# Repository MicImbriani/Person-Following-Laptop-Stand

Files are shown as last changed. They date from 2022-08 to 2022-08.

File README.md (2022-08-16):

# Person-Following Laptop Stand

<h1>Overview</h1>
Built a robot that takes a laptop placed on top, and follows the user left/right and up/down using the laptop's camera.
The purpose for this device is to keep the user centered during online meetings and calls, which are nowadays increasingly more common.
The device uses DC motors for the lateral movement, and a mechanism (a lead scew attached to a DC motor) for the vertical movement.
More details below.

- The 3D modeling was done using Fusion360.
- The models were 3D printed using Cura software, and 3D-printed using Prusa i3 Mk3 printer.
- All wooden parts are in MDF, and were laser cut.
- The code was written in Python and Arduino.
- The electronics' schematics were done using Fritzing.






# The robot is divided into two levels: upper and lower. 

<h2>Lower Level</h2>

LOWER

In the lower level, the wheeilng system is placed: this is used for the left/right movement. Instead of directly attaching the wheels to the motors, a gearing system (2 gears, 1:1 ratio) was used in combination with a 3D-printed component with 2 radial ball bearings in ints inside: this allowed to transfer the weight load from the motors' shafts to the device.
activeWheel
activeWheelOpen

There is also a mechanism (composed of a DC motor and a lead screw) for the up/down movement: this mechanism will move the base at the top of the device on which the laptop is placed.
12motor

Finally, two IR sensors are placed at the extremities of the device, which are used for edge detection and preventing the robot from falling off of the surface on which it is placed.

<h2>Upper Level</h2>
 
UPPERFLOOR

In the upper level, the Arduino, breadboard and AC/DC converter (or, if connecting the robot to an electric outlet is not feasible, a battery) are placed.
Two IR sensors are also placed for preventing the base from moving too high or too low. An extra component is installed to maintain the rotation of the lead screw centred. 


Guiding rods are installed at the four corners of the upper level: their purpose is to maintain the fixed orientation of the base, which  in turn enables the lead screw to move the base up and down. These guiding rods work in combination with the rods that are fixed underneath the laptop base. Additionally, a 3D-printed component is also fixed to enable the transfering of the lead screw's rotational work into linear vertical movement of the base.


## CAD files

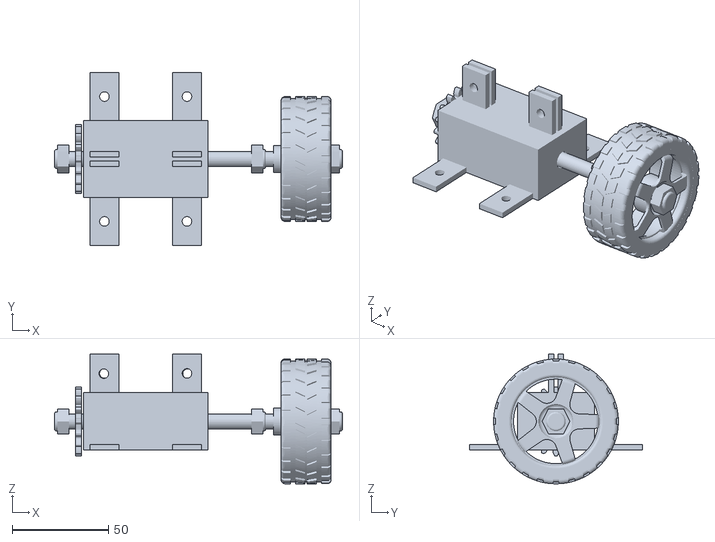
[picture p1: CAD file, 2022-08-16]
CAD Design Files/Wheel System/Active Wheels/ASSEMBLY+Active+Wheels.stl
150.0 x 90.0 x 67.5

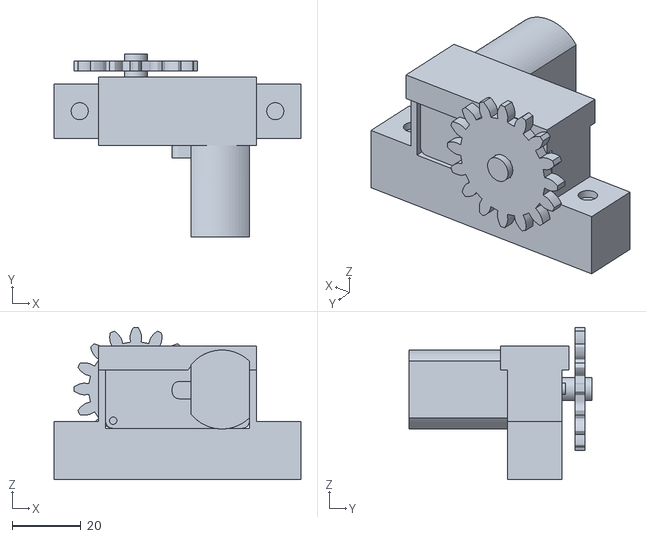
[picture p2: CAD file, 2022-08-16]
CAD Design Files/Wheel System/Motors/ASSEMBLY+motors+and+holders.stl
72.0 x 53.3 x 44.4

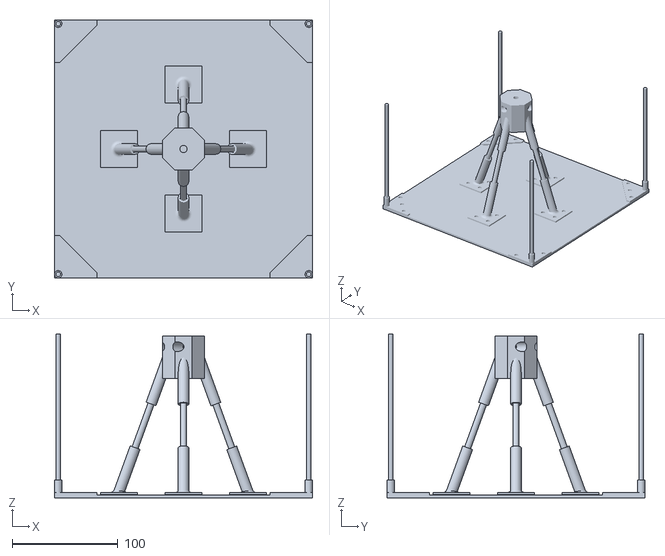
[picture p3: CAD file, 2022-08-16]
CAD Design Files/Upper Floor/ASSEMBLY+Laptop+Base.stl
244.0 x 244.0 x 155.0

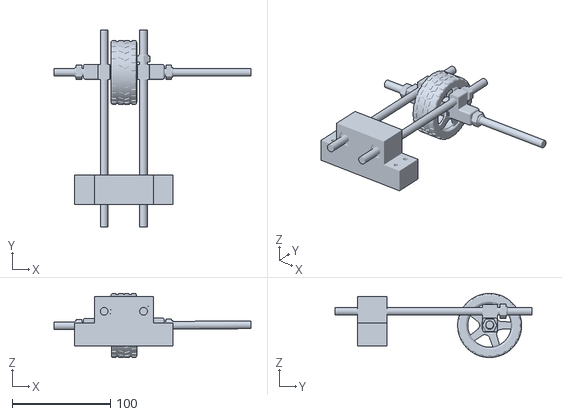
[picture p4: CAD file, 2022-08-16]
CAD Design Files/Wheel System/Passive Wheels/ASSEMBLY+Passive+Wheels.stl
200.0 x 200.0 x 65.1

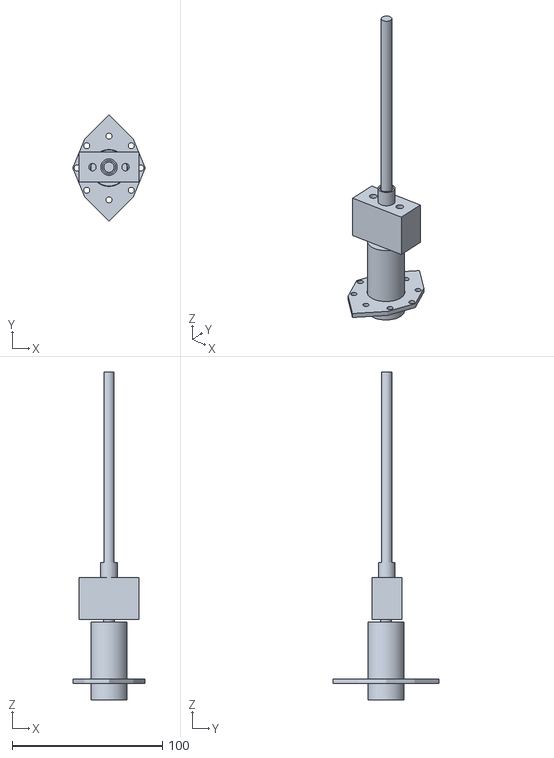
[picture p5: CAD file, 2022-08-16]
CAD Design Files/Lower Floor/Mechanism/ASSEMBLY+Motor+12V.stl
48.1 x 70.7 x 218.5

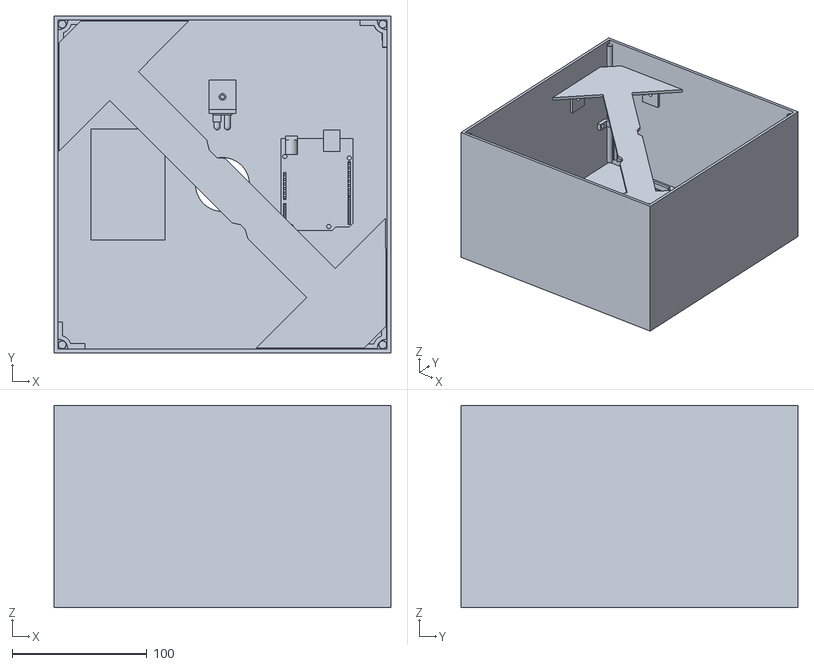
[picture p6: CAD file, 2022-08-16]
CAD Design Files/Upper Floor/ASSEMBLY+Upper+floor.stl
250.0 x 250.0 x 150.0

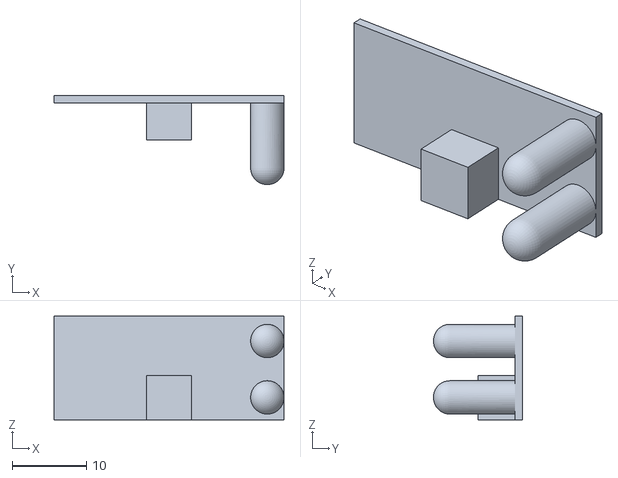
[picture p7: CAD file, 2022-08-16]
CAD Design Files/Lower Floor/IR_sensor.stl
31.0 x 12.0 x 14.0

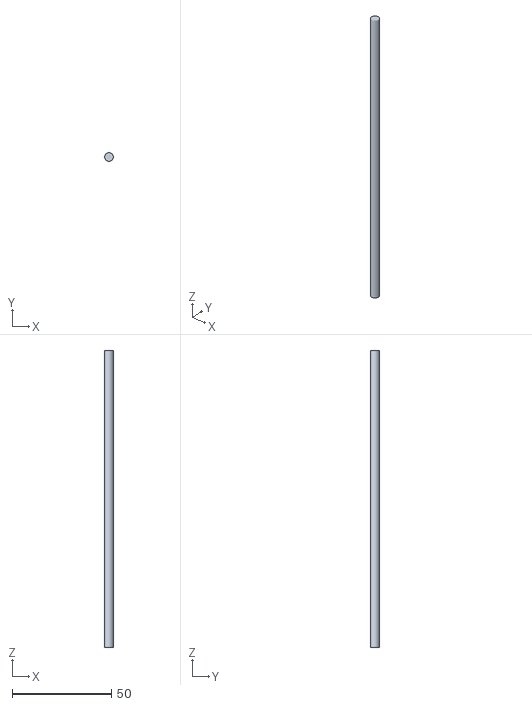
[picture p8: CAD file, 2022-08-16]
CAD Design Files/Upper Floor/Rods.stl
4.40 x 4.40 x 150.0

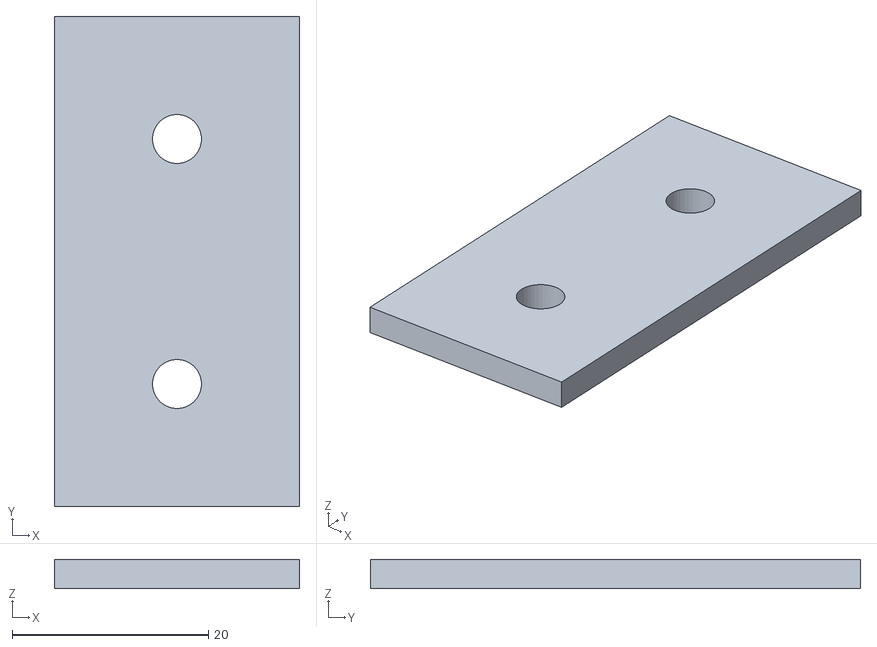
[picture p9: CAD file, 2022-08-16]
CAD Design Files/WallHolder.stl
25.0 x 50.0 x 3.00

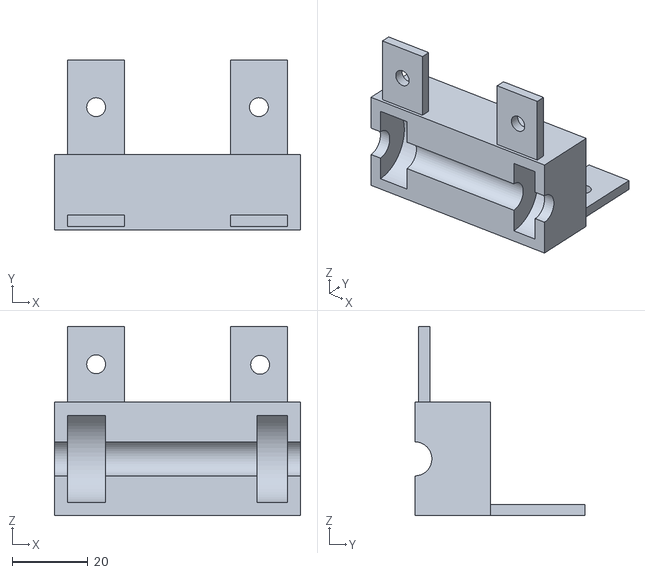
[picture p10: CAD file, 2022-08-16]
CAD Design Files/Wheel System/Active Wheels/BearingsHolder.stl
65.0 x 45.0 x 50.0

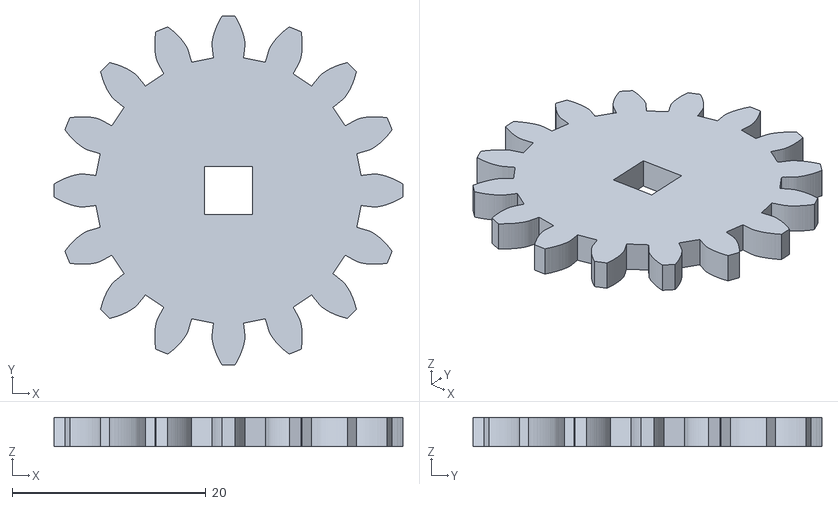
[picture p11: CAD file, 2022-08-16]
CAD Design Files/Wheel System/Motors/Gear+Motor.stl
36.0 x 36.0 x 3.00

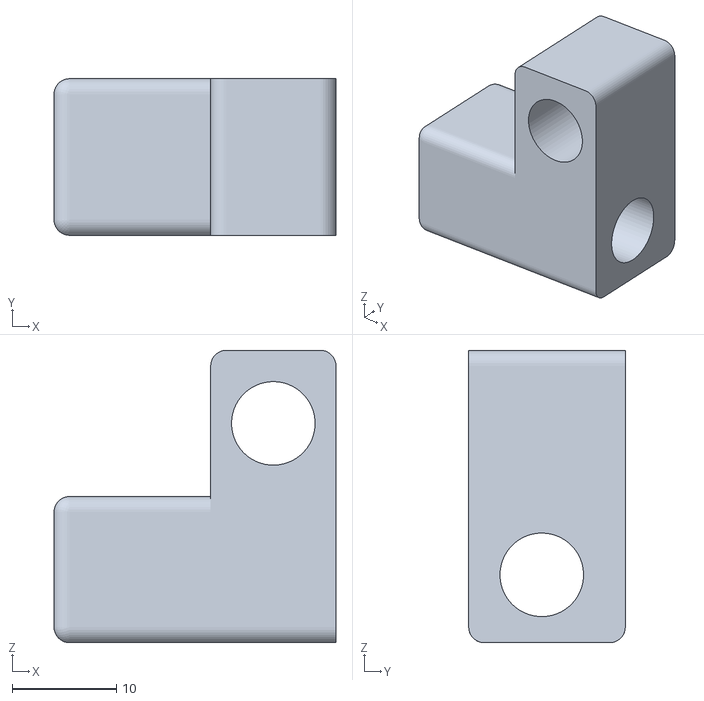
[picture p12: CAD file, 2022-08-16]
CAD Design Files/Wheel System/Passive Wheels/SupportWheelsConnector.stl
27.0 x 15.0 x 28.0

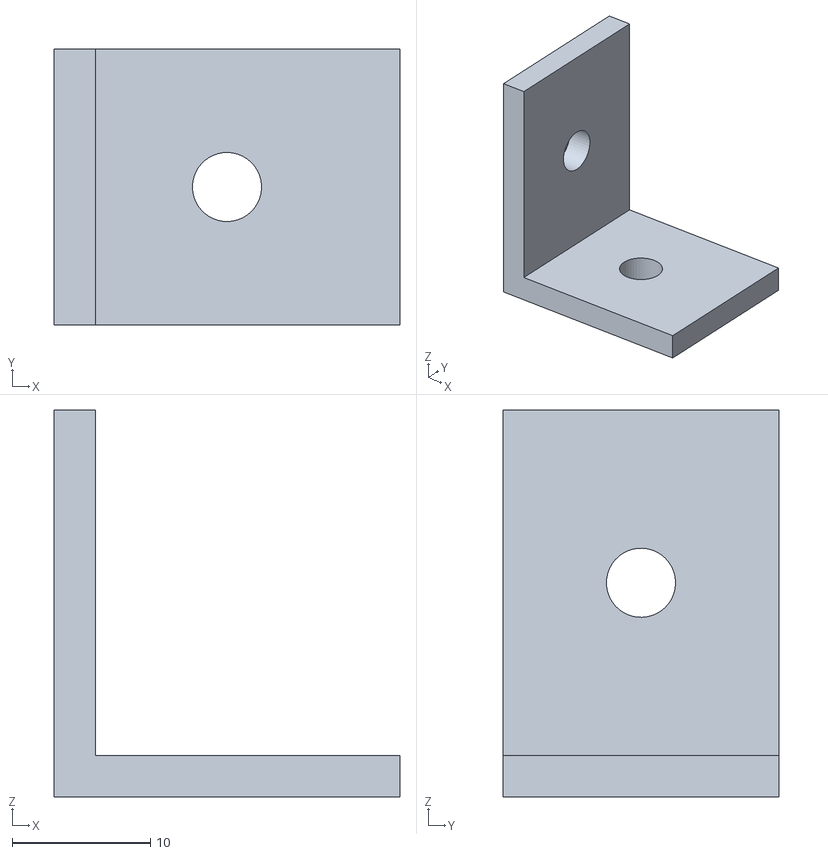
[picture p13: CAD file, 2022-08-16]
CAD Design Files/BaseHolder.stl
25.0 x 20.0 x 28.0

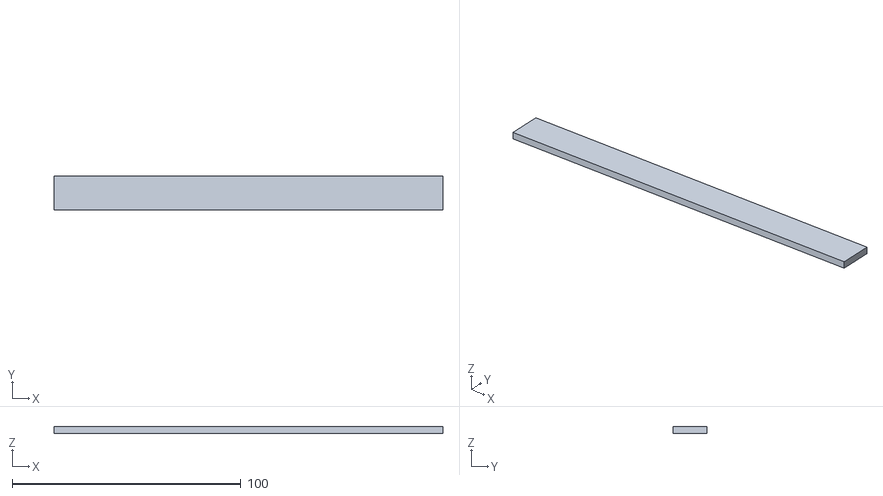
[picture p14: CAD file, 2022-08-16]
CAD Design Files/Lower Floor/IR+Sensor+Stick.stl
170.0 x 15.0 x 3.00

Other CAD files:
CAD Design Files/Lower Floor/Mechanism/ROD+motor+holders.stl
CAD Design Files/Wheel System/Active Wheels/M8+Nut.stl
CAD Design Files/Wheel System/Motors/MotorHoldersSupport.stl
CAD Design Files/Wheel System/Passive Wheels/Wheel.stl
CAD Design Files/Lower Floor/Mechanism/LEAD_SCREW.stl
CAD Design Files/Lower Floor/Mechanism/LeadScrewHolder.stl
CAD Design Files/Lower Floor/Mechanism/LeadScrewRotator.stl
CAD Design Files/Lower Floor/Mechanism/Motor+130RPM12V.stl
CAD Design Files/Lower Floor/Mechanism/MotorHolder_DOWN.stl
CAD Design Files/Lower Floor/Mechanism/MotorHolder_UP.stl
CAD Design Files/Lower Floor/Mechanism/ROD+motor+holder+to+base.stl
CAD Design Files/Upper Floor/ASSEMBLY+Lead+Screw+Stabilizer.stl
CAD Design Files/Upper Floor/Breadboard.stl
CAD Design Files/Upper Floor/GuideRodHeads.stl
CAD Design Files/Upper Floor/GuidelineHolder.stl
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

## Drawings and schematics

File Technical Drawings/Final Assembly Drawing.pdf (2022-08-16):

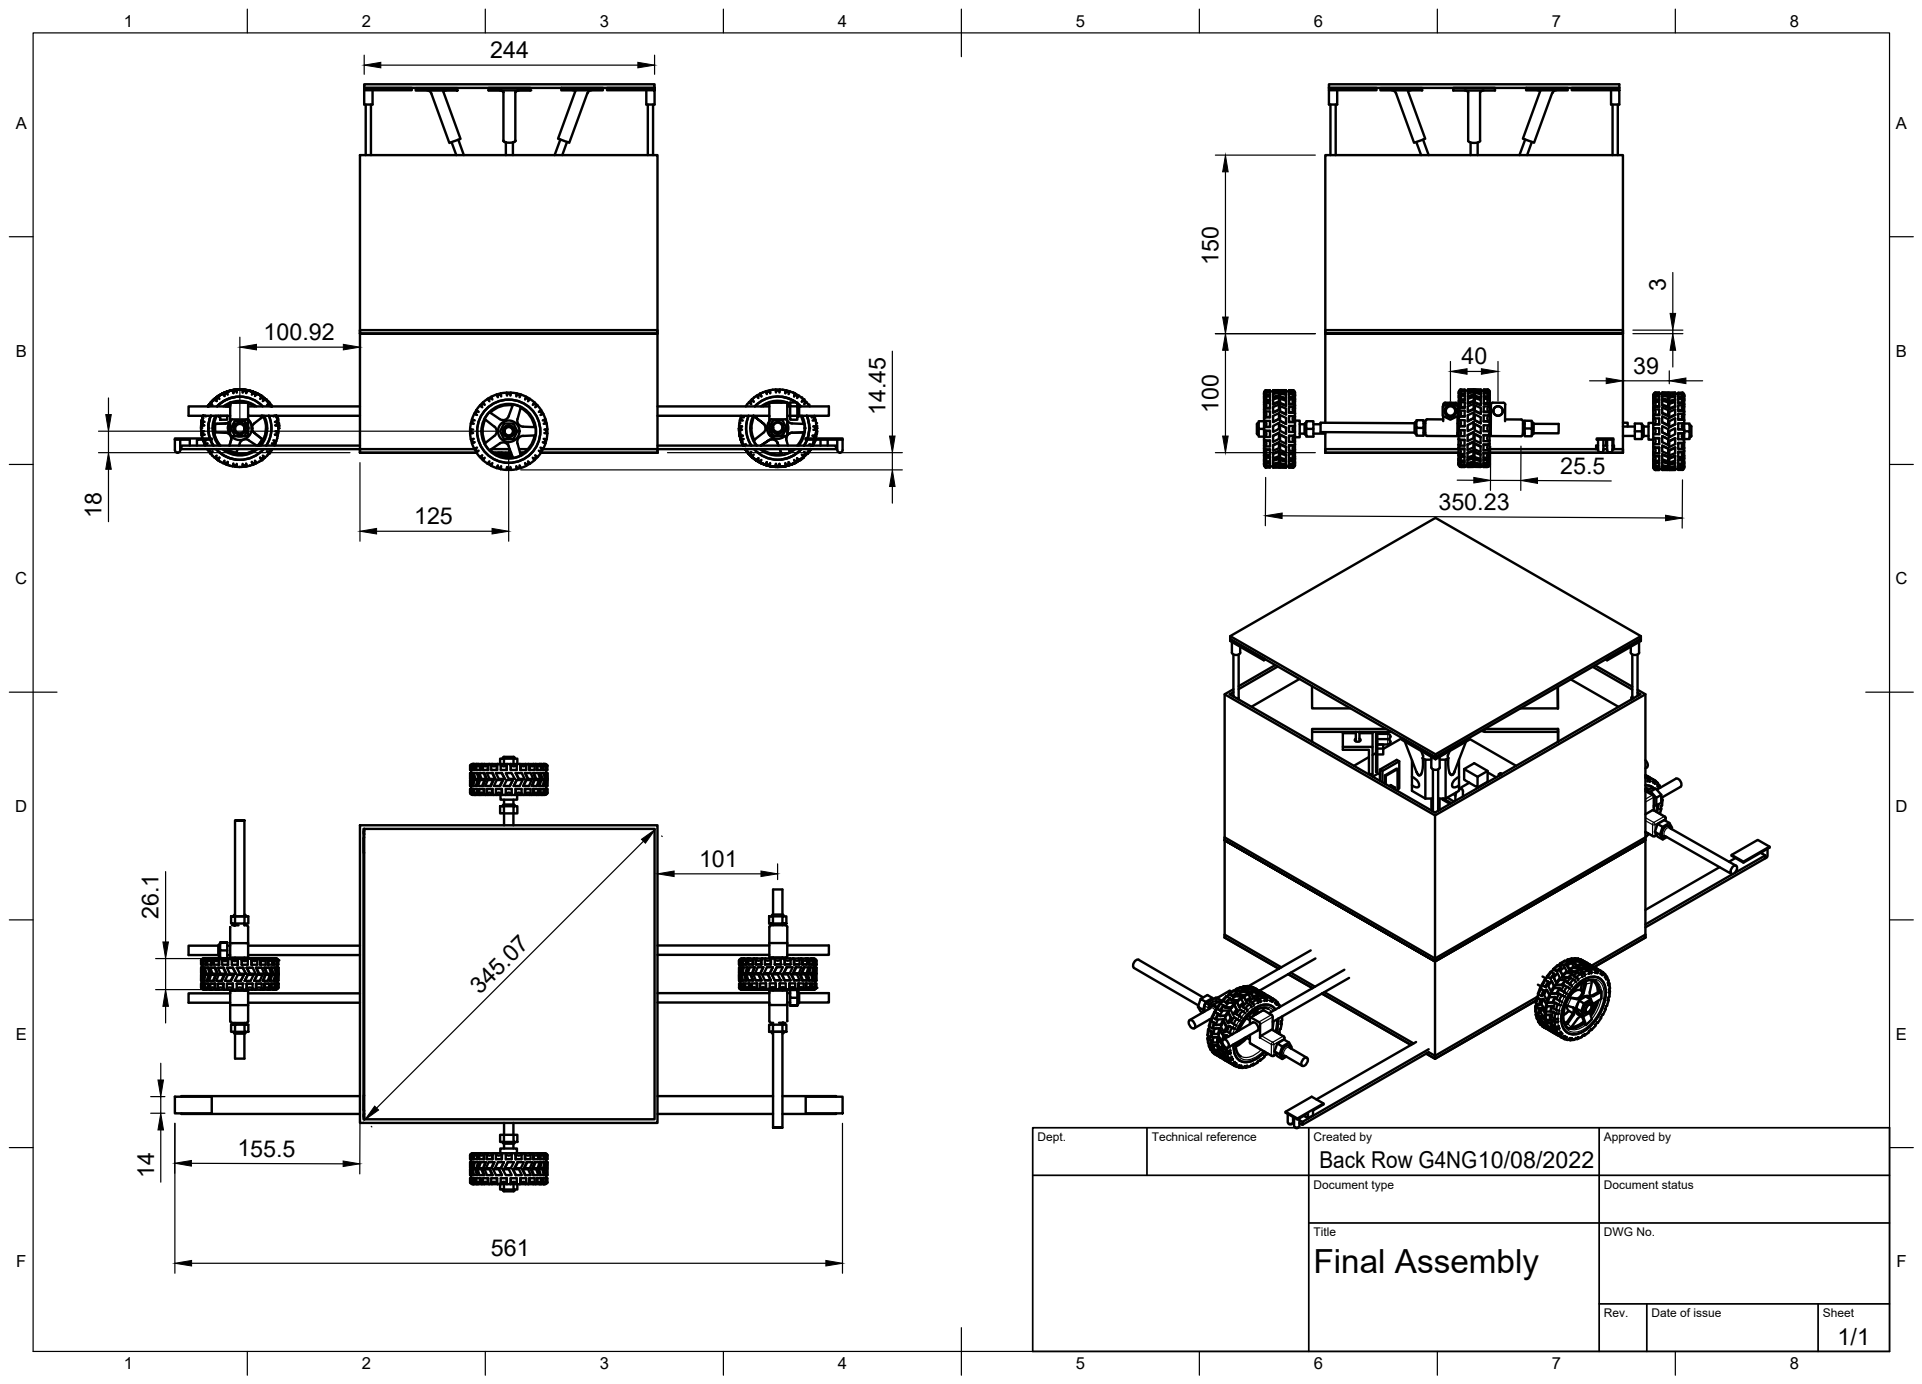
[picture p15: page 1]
Dept.; Technical reference; Created by; Approved by; Document type; Document status; Title; DWG No.; Rev.; Date of issue; Sheet; Final Assembly; Back Row G4NG

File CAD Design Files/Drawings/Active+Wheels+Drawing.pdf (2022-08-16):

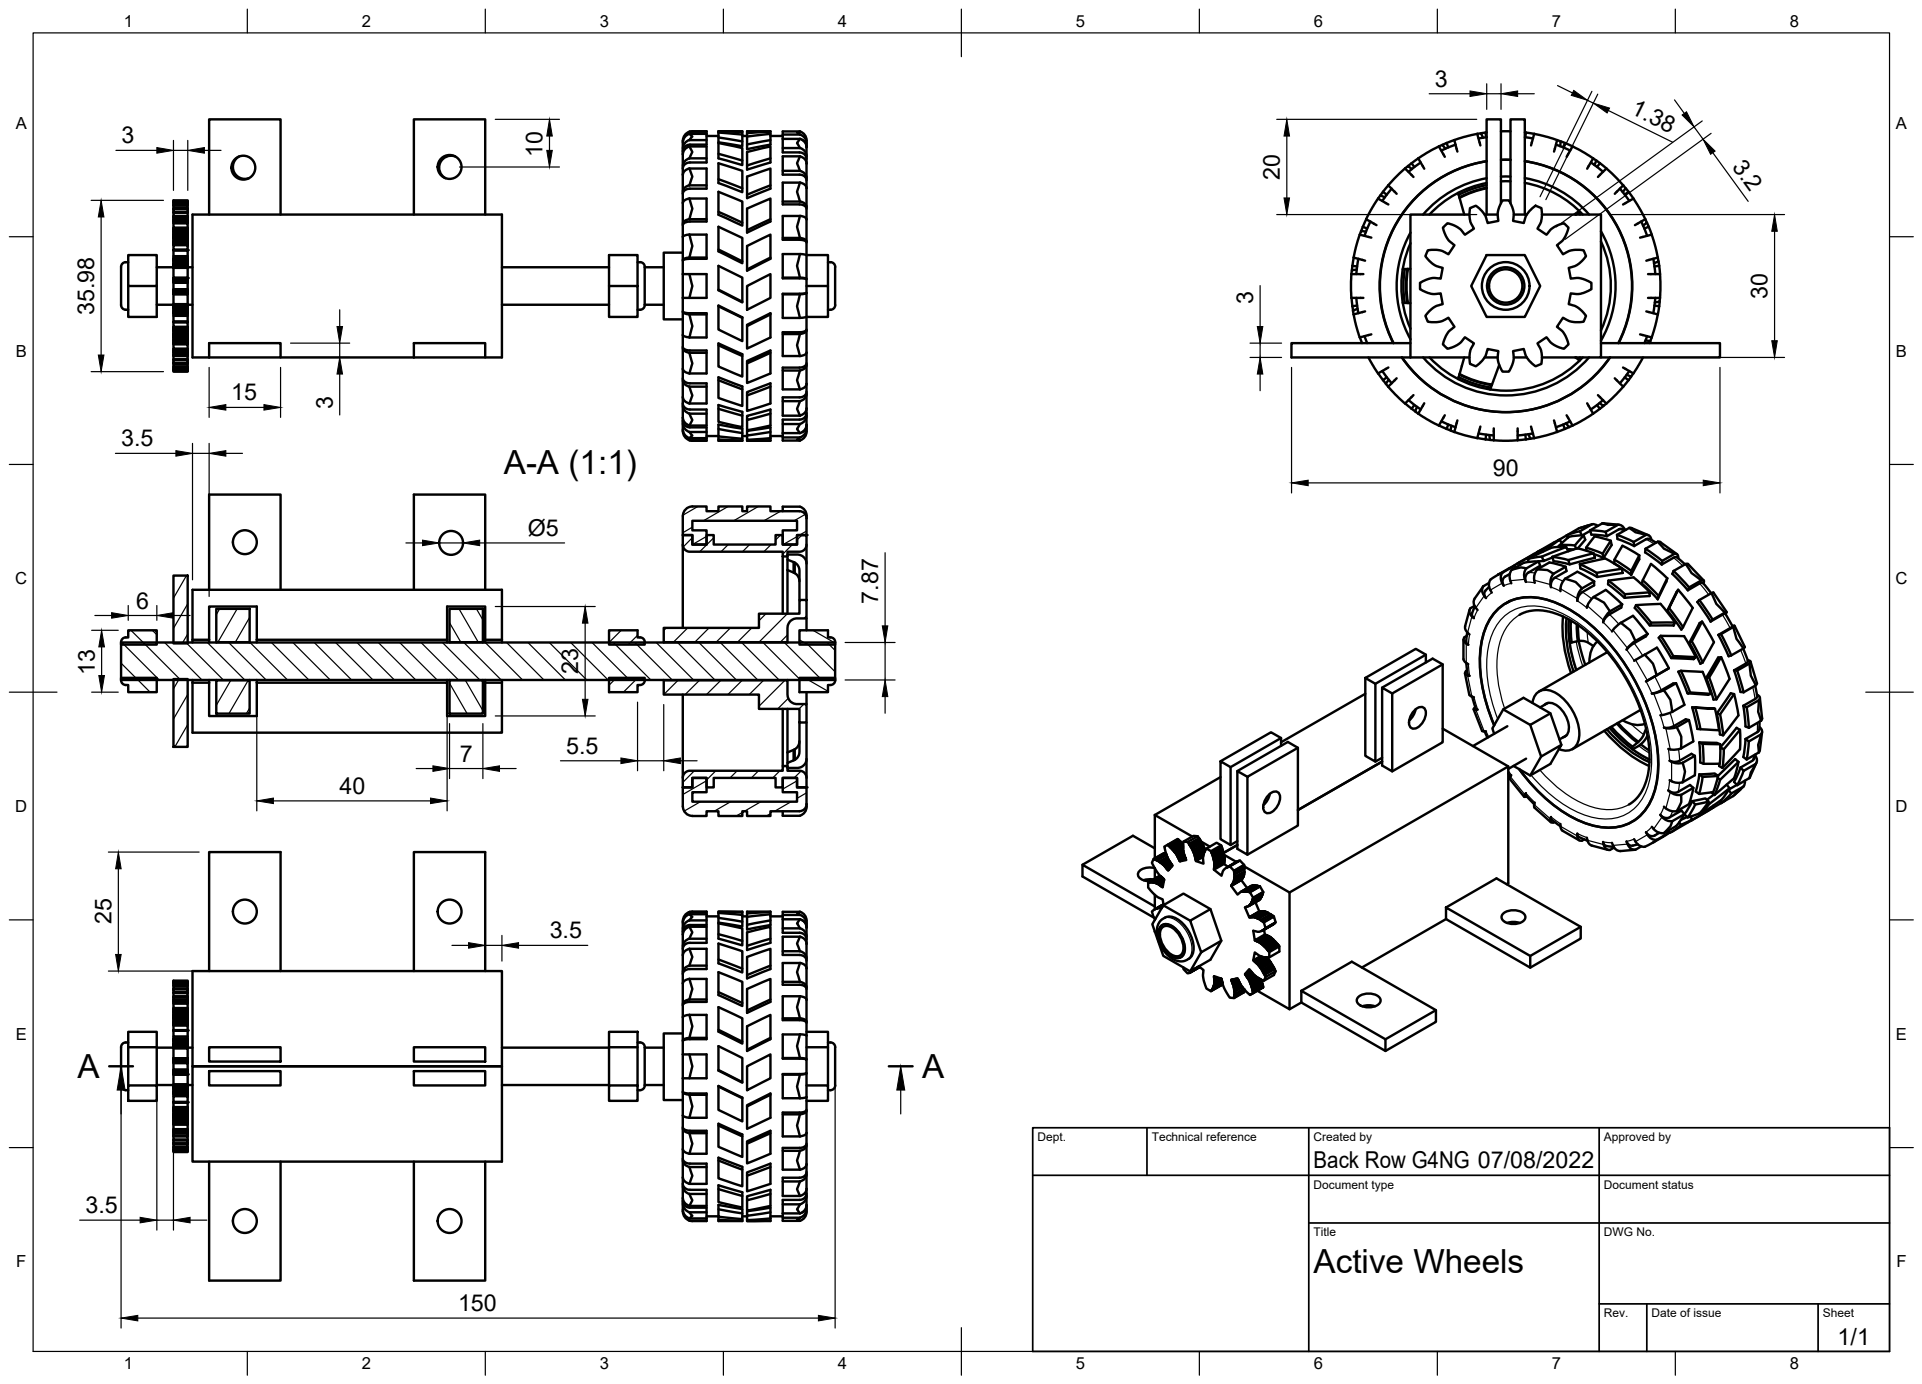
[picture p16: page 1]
Title; DWG No.; Rev.; Date of issue; Sheet; Active Wheels

Dept. | Technical reference | Created by Back Row G4NG 07/08/2022 | Approved by

Document type | Document status

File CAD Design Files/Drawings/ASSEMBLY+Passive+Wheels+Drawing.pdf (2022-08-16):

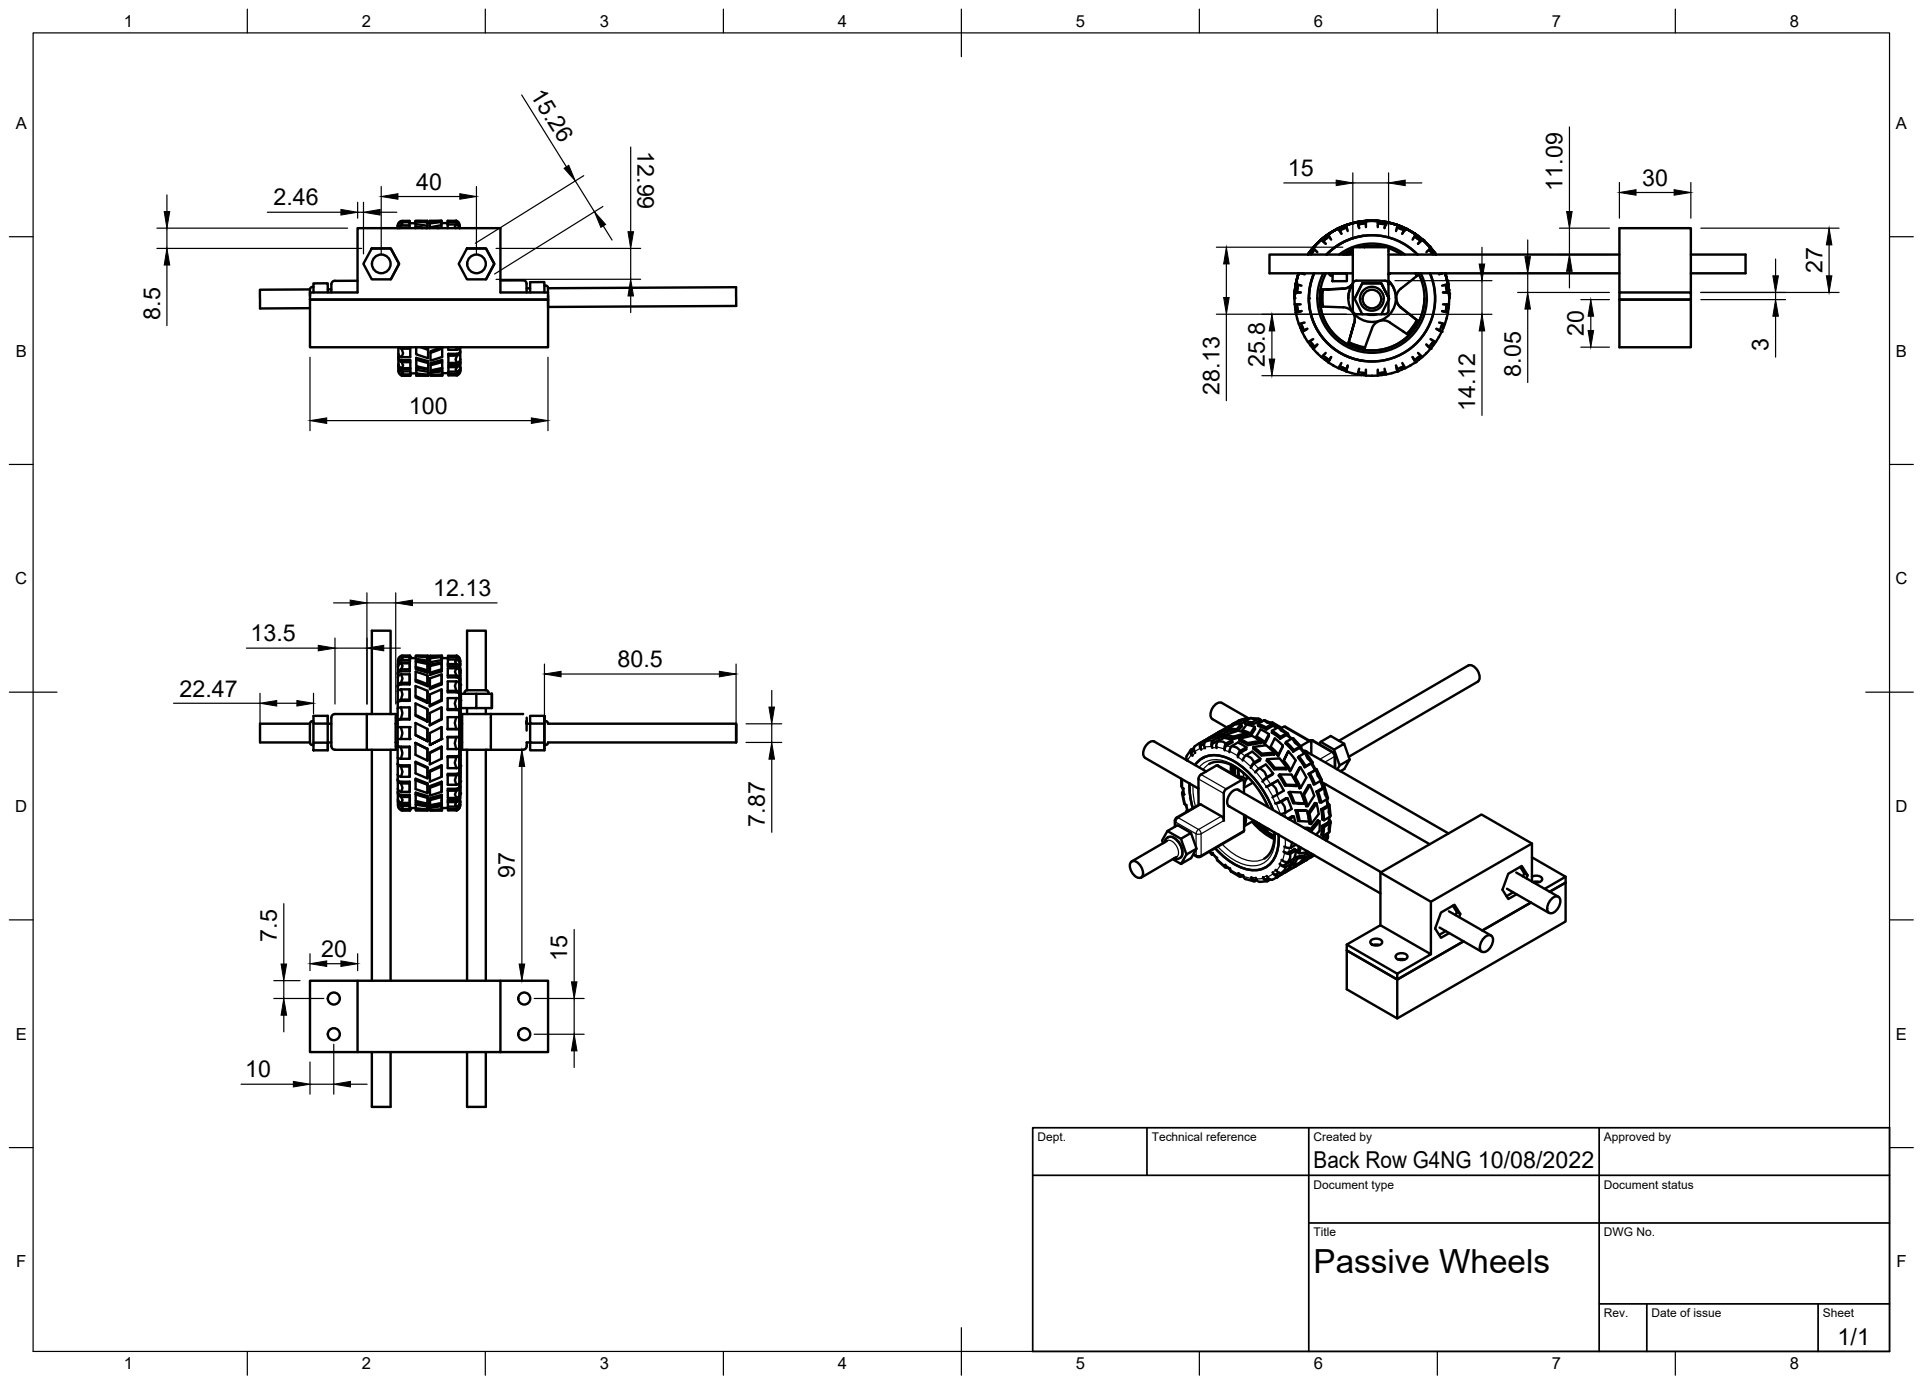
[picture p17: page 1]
Title; DWG No.; Rev.; Date of issue; Sheet; Passive Wheels

Dept. | Technical reference | Created by Back Row G4NG 10/08/2022 | Approved by

Document type | Document status

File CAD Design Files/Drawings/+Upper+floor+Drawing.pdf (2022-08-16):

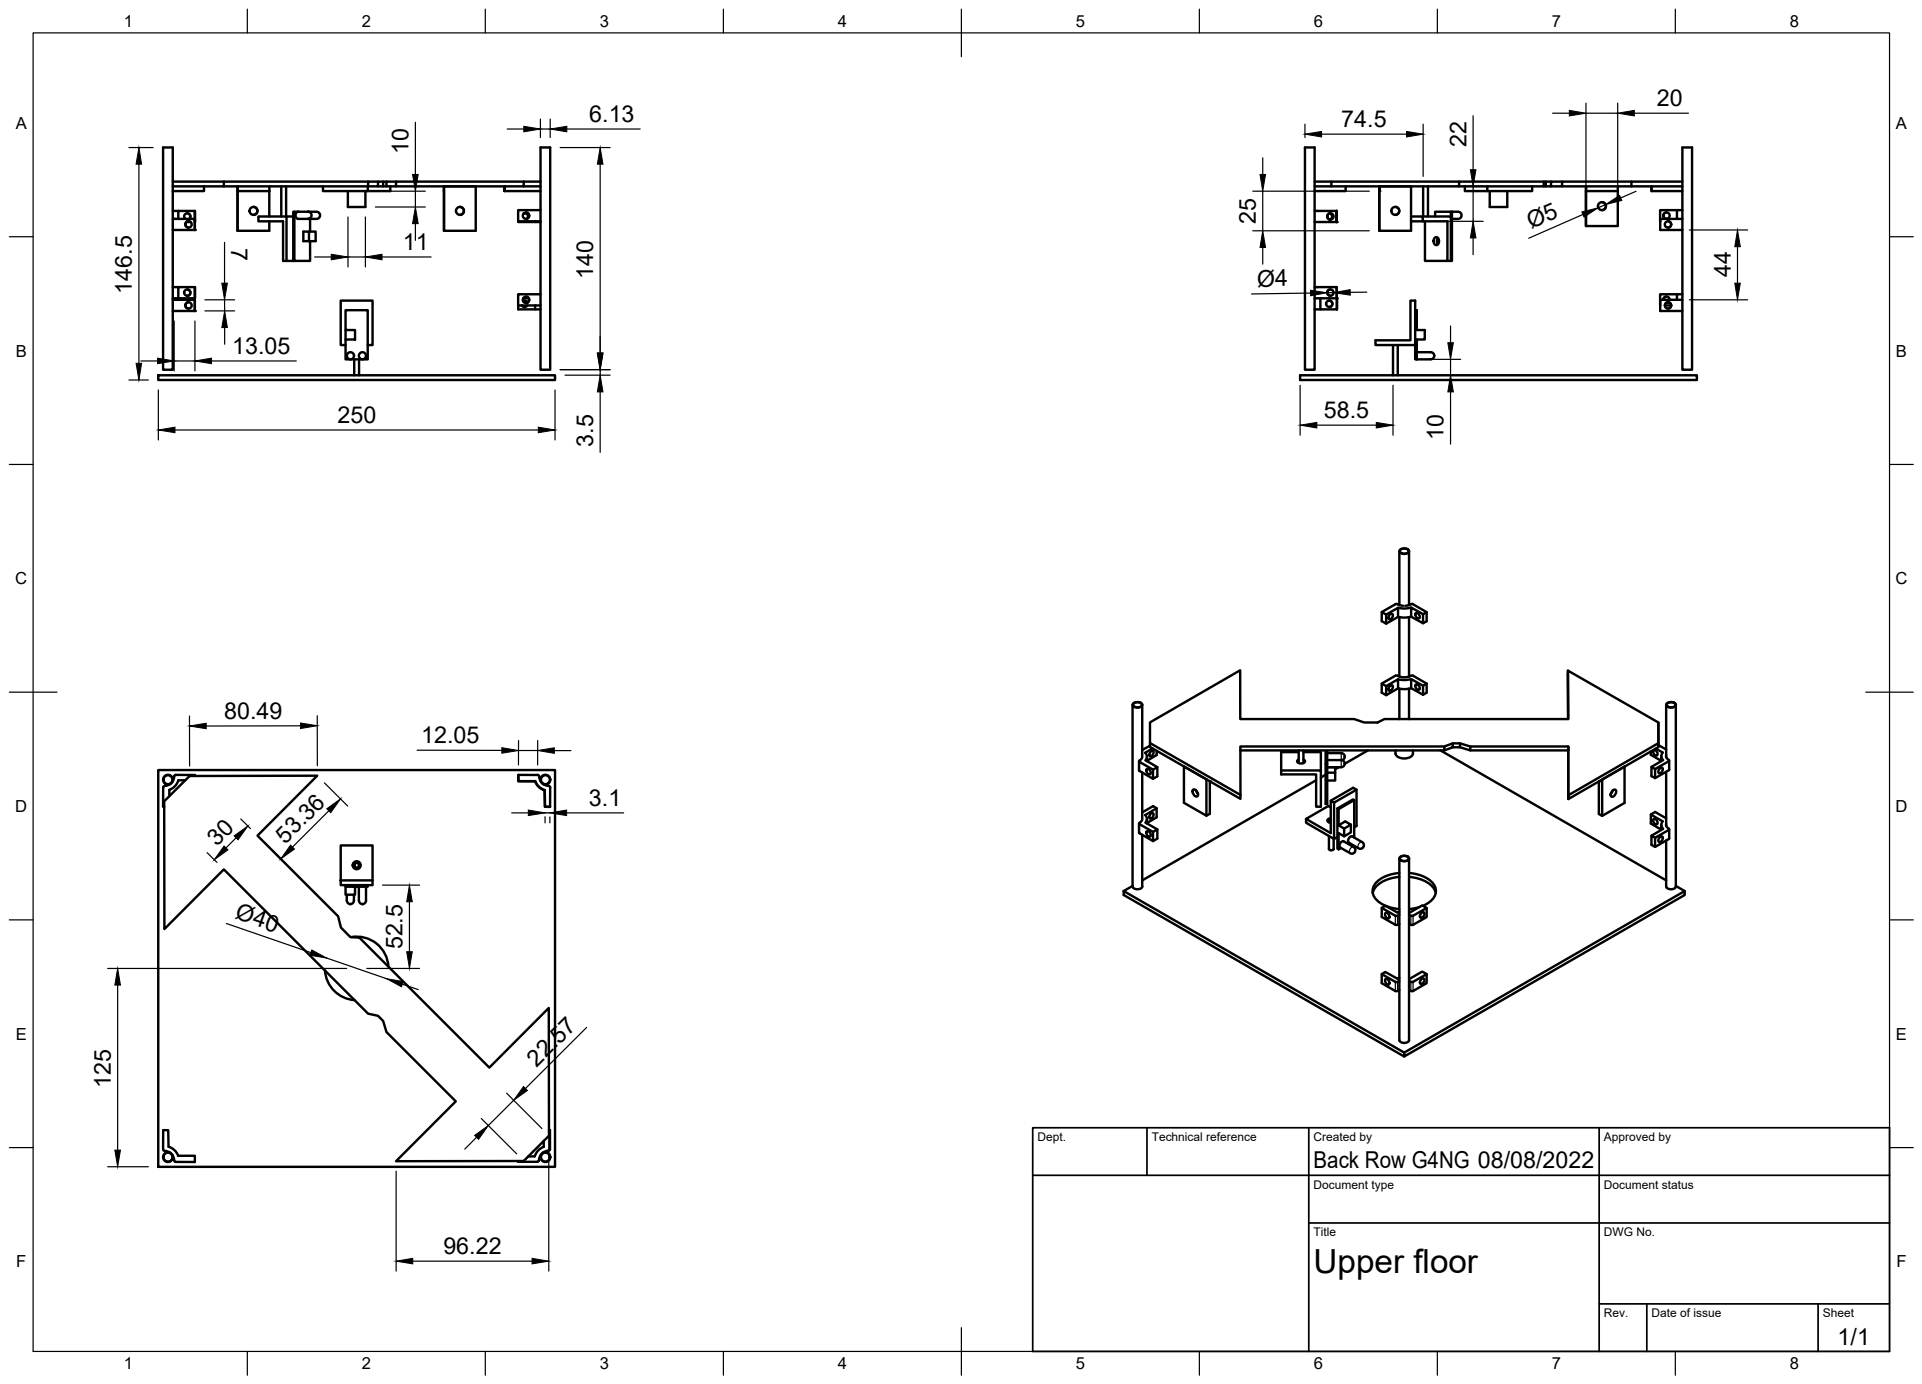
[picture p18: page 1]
Title; DWG No.; Rev.; Date of issue; Sheet; Upper floor

Dept. | Technical reference | Created by Back Row G4NG 08/08/2022 | Approved by

Document type | Document status

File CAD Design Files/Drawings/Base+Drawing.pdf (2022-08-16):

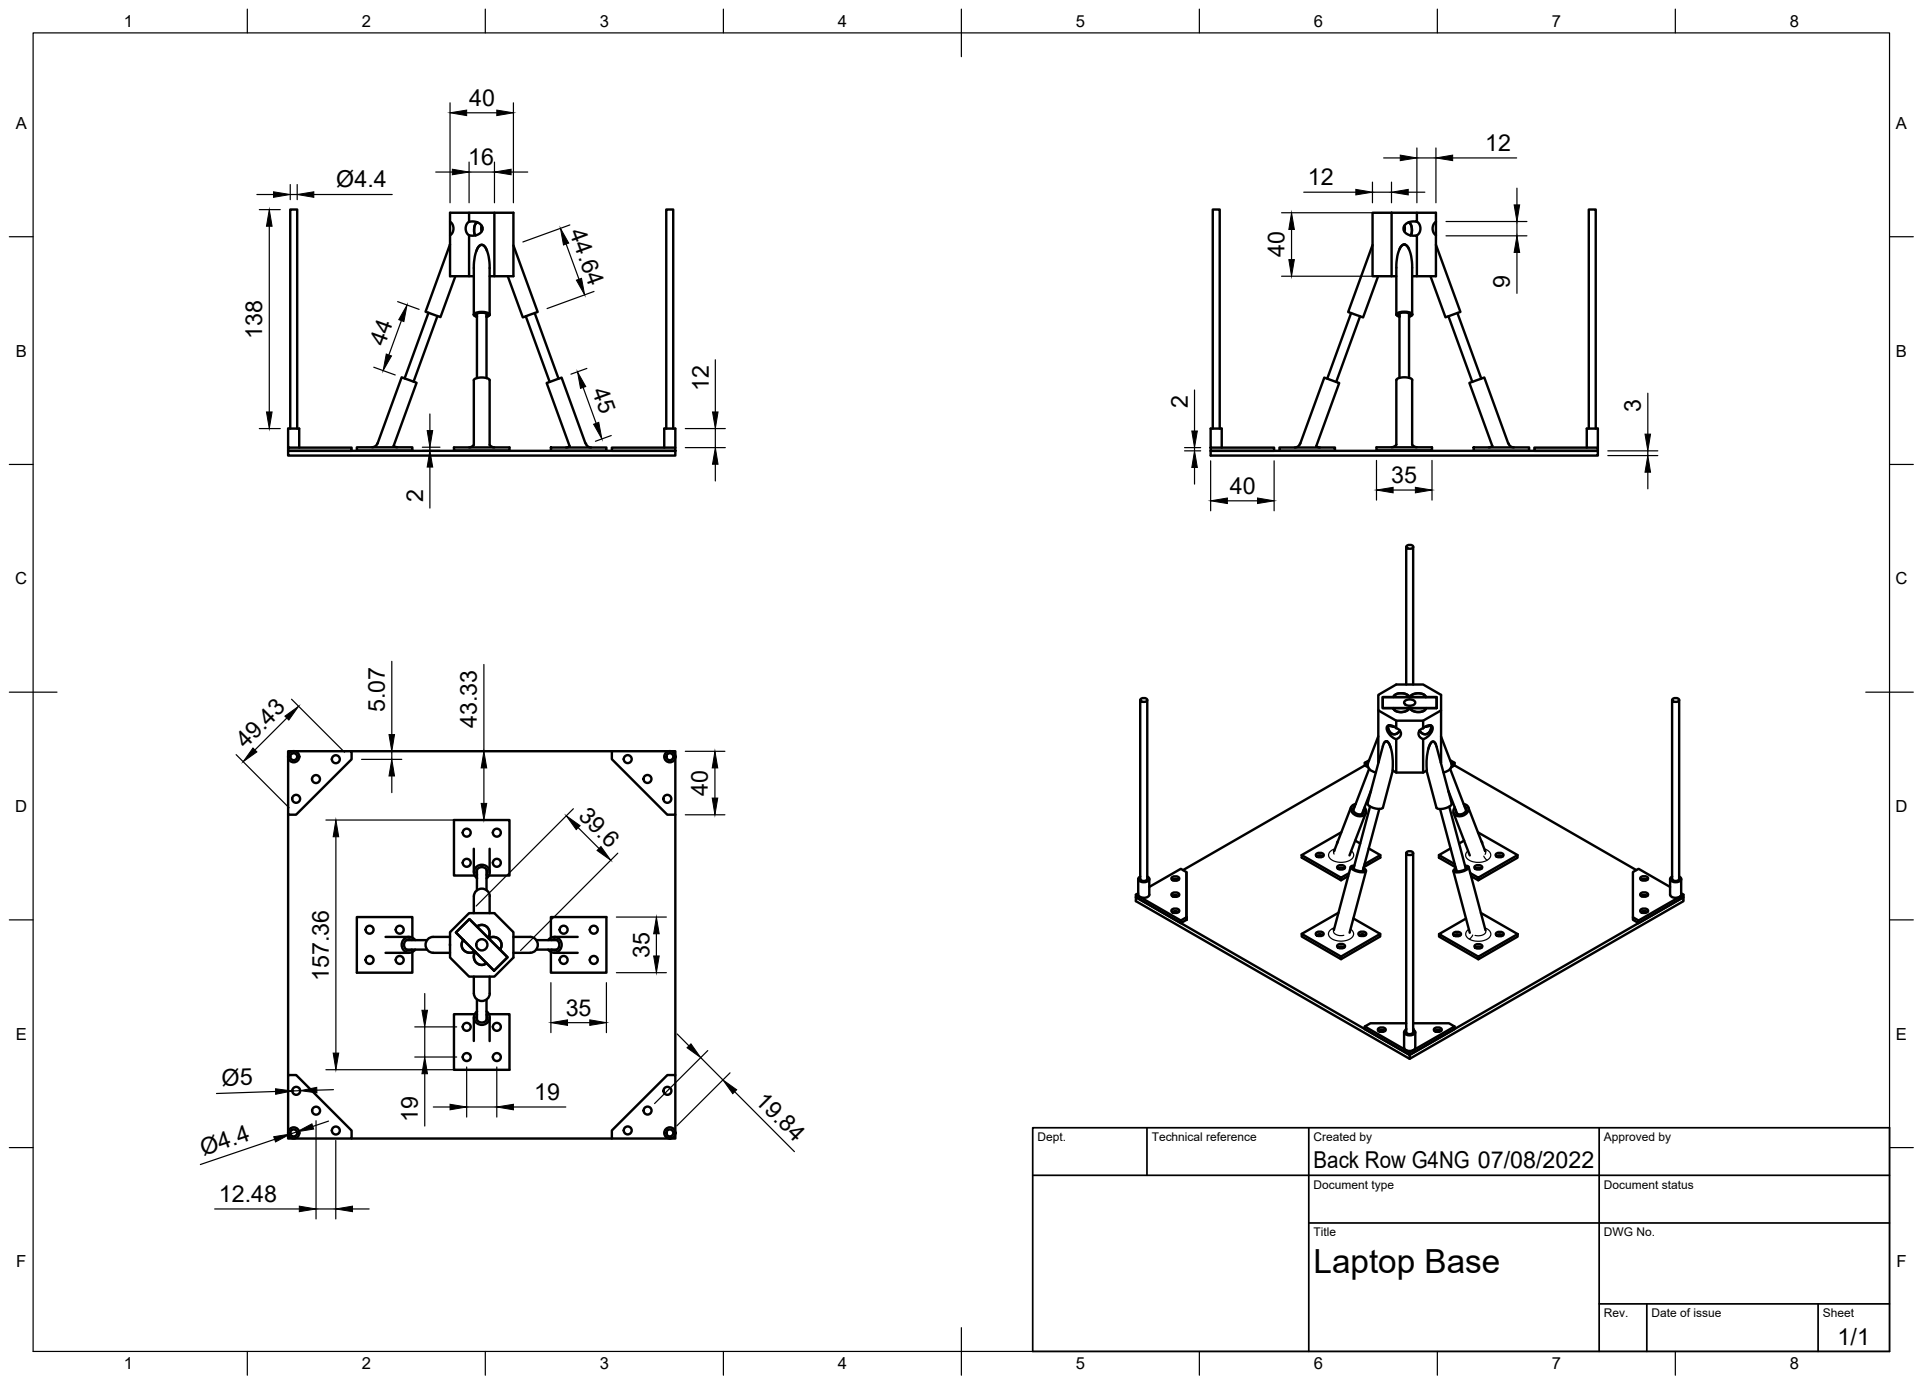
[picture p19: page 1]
8 BCDEF; ABCDEF; Title; DWG No.; Rev.; Date of issue; Sheet; Laptop Base; Back Row G4NG 138

Dept. | Technical reference | Created by 07/08/2022 | Approved by

Document type | Document status

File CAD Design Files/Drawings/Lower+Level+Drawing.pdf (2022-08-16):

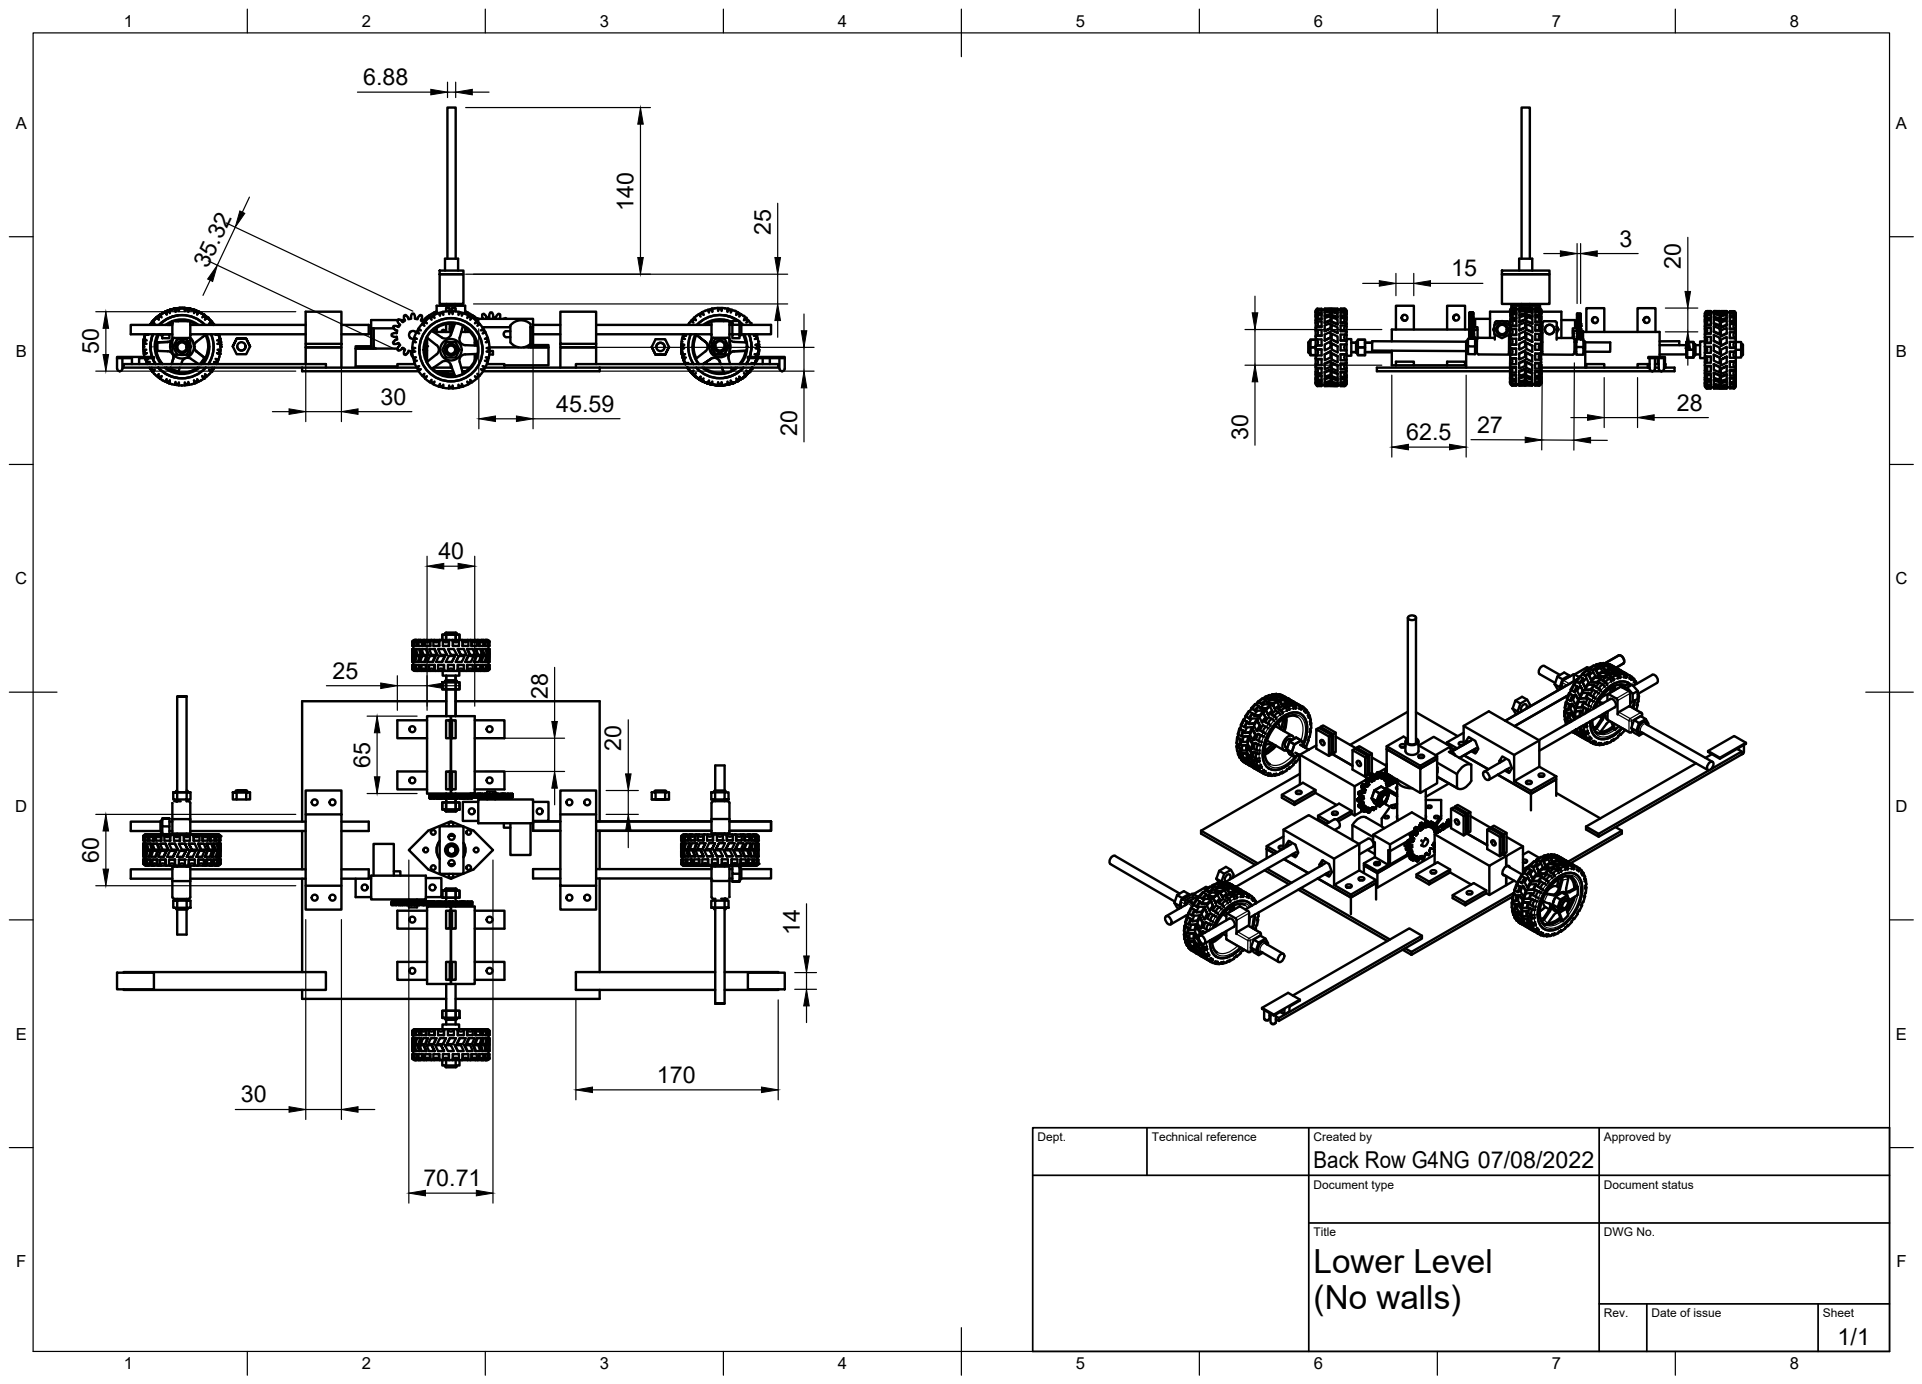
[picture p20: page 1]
Dept.; Technical reference; Created by; Approved by; Document type; Document status; Title; DWG No.; Rev.; Date of issue; Sheet; (No walls); Lower Level; Back Row G4NG 140

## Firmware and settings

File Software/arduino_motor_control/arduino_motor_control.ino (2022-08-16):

// front motor (motor on the left when looking at H-Bridge driver with pins towards you) with OUT1 == GND and OUT2 == VLT:
// motorF_IN1 == HIGH and motorF_IN2 == LOW --> clockwise rotation (rolls to the right)
// motorF_IN1 == LOW and motorF_IN2 == HIGH --> counter clockwise rotation (rolls to the left)
int motorF_IN1 = 8;
int motorF_IN2 = 7;
int motorF_ENA = 9;

// back motor (motor on the right when looking at H-Bridge driver with pins towards you) with OUT3 == VLT and OUT4 == GND:
// motorB_IN3 == HIGH and motorB_IN4 == LOW --> clockwise rotation (rolls to the right)
// motorB_IN3 == LOW and motorB_IN4 == HIGH --> counter clockwise rotation (rolls to the left)
int motorB_IN3 = 5;
int motorB_IN4 = 4;
int motorB_ENB = 3;

// lead screw motor (with PIN3 == VLT and PIN7 == GND):
// motor_IN1 == HIGH and motorL_IN2 == LOW --> clockwise rotation (goes up)
// motor_IN2 == LOW and motorL_IN2 == HIGH --> counter clockwise rotation (goes down)
int motorL_EN12 = 11;
int motorL_IN1 = 12;
int motorL_IN2 = 13;

// infrared sensor for front (right) and back motor (back)
// above threshold == detecting edge --> stop, under threshold == detecting desk--> go
int sensorF_IN = 1;
int sensorB_IN = 0;
//infrared sensor for lead screw motor (up and down)
// above threshold == no white/no lead screw block detected --> go, under threshold == white/lead screw detected --> stop
int sensorU_IN = 2;
int sensorD_IN = 3;

int threshold = 500;

// read IR sensor input
int checkF = 0;
int checkB = 0;
int checkU = 0;
int checkD = 0;

String input_data;


void setup() {
  // put your setup code here, to run once:
  pinMode(sensorF_IN, INPUT);   // OUTPUT??
  pinMode(sensorB_IN, INPUT);   // OUTPUT??

  pinMode(sensorU_IN, INPUT);
  pinMode(sensorD_IN, INPUT);

  pinMode(motorF_IN1, OUTPUT);
  pinMode(motorF_IN2, OUTPUT);
  pinMode(motorF_ENA, OUTPUT);
  
  pinMode(motorB_IN3, OUTPUT);
  pinMode(motorB_IN4, OUTPUT);
  pinMode(motorB_ENB, OUTPUT);

  pinMode(motorL_EN12, OUTPUT);
  pinMode(motorL_IN1, OUTPUT);
  pinMode(motorL_IN2, OUTPUT);

  Serial.begin(115200);
  Serial.setTimeout(1);
}

void loop() {

  checkF = analogRead(sensorF_IN); 
  checkB = analogRead(sensorB_IN);
  checkU = analogRead(sensorU_IN); 
  checkD = analogRead(sensorD_IN);
  
  //set motor speed 
  analogWrite(motorF_ENA, 150);  //60
  analogWrite(motorB_ENB, 150);  //40
  analogWrite(motorL_EN12, 255);
  
  while (!Serial.available());
  input_data = Serial.readString();

  if (input_data == "(-1,-1)"){
    // robot needs to move left and up
    move_left();
    move_up();
    Serial.println("MOVE LEFT AND UP");
  }
    
  else if (input_data == "(0,-1)"){
    // robot needs to move up
    dont_move_horizontally();
    move_up();
    Serial.println("MOVE UP");
  }

  else if (input_data == "(1,-1)"){
    // robot needs to move right and up
    move_right();
    move_up();
    Serial.println("MOVE RIGHT AND UP");
  }
  
  else if (input_data == "(-1,0)"){
    // robot needs to move left
    dont_move_vertically();
    move_left();
    Serial.println("MOVE LEFT");
  }
    
  else if (input_data == "(0,0)"){
    // robot needs to stop / does not need to move
    stand_still();
    Serial.println("DON'T MOVE");
  }

  else if (input_data == "(1,0)"){
    // robot needs to move right
    dont_move_vertically();
    move_right();
    Serial.println("MOVE RIGHT");
  }

  else if (input_data == "(-1,1)"){
    // robot needs to move left and down
    move_left();
    move_down();
    Serial.println("MOVE LEFT AND DOWN");
  }

  else if (input_data == "(0,1)"){
    // robot needs to move down
    dont_move_horizontally();
    move_down();
    Serial.println("MOVE DOWN");
  }

  else if (input_data == "(1,1)"){
    // robot needs to move right and down
    move_right();
    move_down();
    Serial.println("MOVE RIGHT AND DOWN");
  }

  else {
    // no need to move as face is centered
    stand_still();
  }
}



////////////// UTILITY FUNCTIONS //////////////////

bool edge_detection() {
//checks if sensorF and/or sensorB detect edge
  if ((checkF > threshold) || (checkB > threshold)){
    return true;
  }
  else {
    return false;
  }
}

bool top_detection(){
//checks if sensorU detects top
  if (checkU < threshold){
    return true;
  }
  else {
    return false;
  }
}

bool bottom_detection(){
//checks if sensorD detects bottom
  if (checkD < threshold){
    return true;
  }
  else {
    return false;
  }
}

void dont_move_horizontally() {
// stops motorF and motorB
  digitalWrite(motorF_IN1, LOW);
  digitalWrite(motorF_IN2, LOW);

  digitalWrite(motorB_IN3, LOW);
  digitalWrite(motorB_IN4, LOW);
}

void dont_move_vertically(){
// stops motorL
  digitalWrite(motorL_IN1, LOW);
  digitalWrite(motorL_IN2, LOW);
}

void stand_still() {
// stops motorF, motorB and motorL
  digitalWrite(motorF_IN1, LOW);
  digitalWrite(motorF_IN2, LOW);

  digitalWrite(motorB_IN3, LOW);
  digitalWrite(motorB_IN4, LOW);

  digitalWrite(motorL_IN1, LOW);
  digitalWrite(motorL_IN2, LOW);
  Serial.println("NO NEED TO MOVE");
}


void move_left() {
  Serial.println(edge_detection());
  if (not edge_detection()){
    digitalWrite(motorF_IN1, LOW);
    digitalWrite(motorF_IN2, HIGH);

    digitalWrite(motorB_IN3, LOW);
    digitalWrite(motorB_IN4, HIGH);
    Serial.println("MOVE LEFT");  
  }
  else {
    dont_move_horizontally();
    Serial.println("CANNOT MOVE LEFT --> DETECTED EDGE");
  }
}

void move_right() {
  if (not edge_detection()){
    Serial.println("IF");
    digitalWrite(motorF_IN1, HIGH);
    digitalWrite(motorF_IN2, LOW);
  
    digitalWrite(motorB_IN3, HIGH);
    digitalWrite(motorB_IN4, LOW);
    Serial.println("MOVE RIGHT");
  }
  else {
    Serial.println("ELSE");
    dont_move_horizontally();
    Serial.println("CANNOT MOVE RIGHT --> DETECTED EDGE");
  }
}

void move_up() {
  if (not top_detection()){
    digitalWrite(motorL_IN1, HIGH);
    digitalWrite(motorL_IN2, LOW);
    Serial.println("MOVE UP");
  }
  else {
    dont_move_vertically();
    Serial.println("CANNOT MOVE UP --> REACHED TOP");
  }
}

void move_down() {
  if (not bottom_detection()) {
    digitalWrite(motorL_IN1, LOW);
    digitalWrite(motorL_IN2, HIGH);
    Serial.println("MOVE DOWN");
  }
  else {
    dont_move_vertically();
    Serial.println("CANNOT MOVE DOWN --> REACHED BOTTOM");
  }
}

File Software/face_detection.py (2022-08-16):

import cv2
import serial

arduino = serial.Serial(port='COM3', baudrate=115200, timeout=.1) # adapt to your Arduino port

# Get user supplied values
cascPath = "haarcascade_frontalface_default.xml"

# Create the haar cascade
faceCascade = cv2.CascadeClassifier(cascPath)

# Read the video
video_capture = cv2.VideoCapture(0)


while True:
    # Capture frame-by-frame
    ret, frame = video_capture.read()

    gray = cv2.cvtColor(frame, cv2.COLOR_BGR2GRAY)

    # Detect faces in the image
    faces = faceCascade.detectMultiScale(
        gray,
        scaleFactor=1.1,
        minNeighbors=5,
        minSize=(100, 100),
        flags=cv2.CASCADE_SCALE_IMAGE
    )

    # Draw a rectangle around the faces
    for (x, y, w, h) in faces:
        x_center_frame = int(320 - (w / 2))
        y_center_frame = int(240 - (h / 2))

        threshold = h / 3

        # conditions
        # point (x,y)=(0,0) is in the upper left corner of video frame
        x_centered = x_center_frame - threshold <= x <= x_center_frame + threshold
        x_too_left = x < x_center_frame - threshold
        x_too_right = x > x_center_frame + threshold
        y_centered = y_center_frame - threshold <= y <= y_center_frame + threshold
        y_too_up = y < y_center_frame - threshold
        y_too_down = y > y_center_frame + threshold

        # we encode the video frame for communication between the Python and Arduino code as follows:
        # we define the required movements based on the robot starting from position (0,0)
        # _____________________________
        # | (-1,-1) | (0,-1) | (1,-1) |
        # -----------------------------
        # |  (-1,0) |  (0,0) |  (1,0) |
        # -----------------------------
        # |  (-1,1) |  (0,1) |  (1,1) |
        # -----------------------------
        if x_too_left and y_too_up:
            # person is in position (-1,-1) --> robot needs to move left and up
            arduino.write(bytes("(-1,-1)", 'utf-8'))
            cv2.rectangle(frame, (x, y), (x + w, y + h), (0, 0, 255), 2)
        elif x_centered and y_too_up:
            # person is in position (0,-1) --> robot needs to move up
            arduino.write(bytes("(0,-1)", 'utf-8'))
            cv2.rectangle(frame, (x, y), (x + w, y + h), (0, 0, 255), 2)
        elif x_too_right and y_too_up:
            # person is in position (1,-1) --> robot needs to move right and up
            arduino.write(bytes("(1,-1)", 'utf-8'))
            cv2.rectangle(frame, (x, y), (x + w, y + h), (0, 0, 255), 2)
        elif x_too_left and y_centered:
            # person is in position (-1,0) --> robot needs to move left
            arduino.write(bytes("(-1,0)", 'utf-8'))
            cv2.rectangle(frame, (x, y), (x + w, y + h), (0, 0, 255), 2)
        elif x_centered and y_centered:
            # person is in position (0,0) --> robot does not need to move
            arduino.write(bytes("(0,0)", 'utf-8'))
            cv2.rectangle(frame, (x, y), (x + w, y + h), (0, 255, 0), 2)
        elif x_too_right and y_centered:
            # person is in position (1,0) --> robot needs to move right
            arduino.write(bytes("(1,0)", 'utf-8'))
            cv2.rectangle(frame, (x, y), (x + w, y + h), (0, 0, 255), 2)
        elif x_too_left and y_too_down:
            # person is in position (-1,1) --> robot needs to move left and down
            arduino.write(bytes("(-1,1)", 'utf-8'))
            cv2.rectangle(frame, (x, y), (x + w, y + h), (0, 0, 255), 2)
        elif x_centered and y_too_down:
            # person is in position (0,1) --> robot needs to move down
            arduino.write(bytes("(0,1)", 'utf-8'))
            cv2.rectangle(frame, (x, y), (x + w, y + h), (0, 0, 255), 2)
        elif x_too_right and y_too_down:
            # person is in position (1,1) --> robot needs to move right and down
            arduino.write(bytes("(1,1)", 'utf-8'))
            cv2.rectangle(frame, (x, y), (x + w, y + h), (0, 0, 255), 2)
        
        print(arduino.readline())

        cv2.putText(frame, f"x_center: {x_center_frame}, x: {x}, y_center: {y_center_frame}, y: {y}",
                    (10, frame.shape[0] - 10), cv2.FONT_HERSHEY_SIMPLEX, 0.35, (0, 0, 255), 1)

    cv2.imshow("Video", frame)

    if cv2.waitKey(1) & 0xFF == ord('q'):
        break

# When everything is done, release the capture
video_capture.release()
cv2.destroyAllWindows()
